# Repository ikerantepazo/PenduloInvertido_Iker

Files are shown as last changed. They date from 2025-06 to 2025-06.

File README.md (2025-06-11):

# PenduloInvertido_Iker
En este repositorio se encuentra tanto la práctica 4 cómo la práctica 6 de la asignatura de Teoría de Control

PRÁCTICA 4 - *PID en tiempo discreto*

Esta práctica tiene como objetivo implementar una biblioteca de controladores PID en tiempo discreto para ser utilizada en un microcontrolador ESP32, con aplicación directa en el control de un péndulo invertido. Esta biblioteca será utilizada en el desarrollo del proyecto de control descrito en el capítulo 6 del guión de prácticas.

Se desarrollarán tres variantes del controlador PID en tiempo discreto:

-PID : utiliza aproximaciones hacia atrás para las derivadas y sumas acumulativas para la integral.
-PID como filtro IIR: modelado mediante transformada Z, facilitando su implementación como filtro digital.
-PID filtro baja : se le pone un filtro al término derivativo para evitar que el ruido o los cambios bruscos del error afecten al control.

Cada implementación está basada en los pseudocódigos del guión.

Esta práctica está encapsulada en la carpeta libraries donde nos encontraremos :

I2Cdev/

Contiene archivos fuente y cabeceras que permiten la comunicación mediante el protocolo I2C. Es una biblioteca comúnmente usada para facilitar la lectura y escritura con sensores como el MPU6050

MPU6050/

Incluye las definiciones y funciones específicas para el sensor MPU6050, que proporciona mediciones de aceleración y giroscopio. Esta biblioteca se apoya en I2Cdev para obtener los datos del sensor y es esencial para calcular la posición y velocidad angular del péndulo.

PIDController/

Es la biblioteca desarrollada para está práctica para implementar los tres tipos de controladores PID discretos:

-PID directo
-PID como filtro IIR
-PID filtro pasa baja

Dentro de cada carpeta estarán los archivos .h y .cpp con la implementación de las clases PID

Se añadirá además una carpeta examples que contendrá tres ejemplos simples que muestran cómo usar cada una de las variantes del controlador PID implementadas.

CodigoCompletoPendulo.ino

Este es el sketch código principal de Arduino que integra las bibliotecas anteriores. Aquí se encuentra el código de control que:

-Lee el ángulo del péndulo usando el MPU6050
-Calcula la señal de control con el PID
-Aplica la corrección al actuador
-Permite probar y comparar las distintas variantes del controlador PID

PRÁCTICA 6 - **PENDULO INVERTIDO**

Iker Antepazo Cancelas 

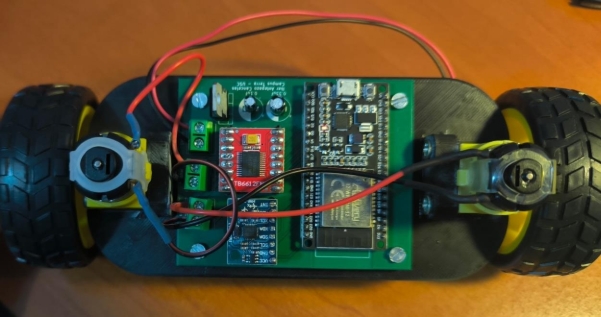
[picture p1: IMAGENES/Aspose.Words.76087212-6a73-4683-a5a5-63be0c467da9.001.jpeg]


**Introducción:**
**\
` `En este documento recogeremos el proceso llevado a cabo para la creación y construcción de un robot llamado “péndulo invertido”, cuya función será de tratar de mantenerse en posición vertical con una tolerancia de ±5◦. 

El sistema debe compensar los empujones externos y volver a la posición vertical y debe ser capaz de poder iniciar su funcionamiento desde cualquier posición. 

**Metodología seguida**

1. **Buscar proyectos similares:** Investigar si ya existe un proyecto de un robot similar que sea funcional y esté documentado. Tanto en respositorios de github como en mi caso en videos de la plataforma YouTube y en la página “grabcad”. 
1. **Investigación general:** Como no existe ningún proyecto bien hecho y bien documentado que esté completo, procedemos a investigar el modus operandi que trataremos de llevar a cabo el proyecto partiendo de las ideas que sacamos de los sitios web antes mencionados. 
3. **Fijación de objetivos:** Es importante la fijación de ciertas metas para saber qué hardware necesitamos. Tanto es así para nuestro chasis como para nuestra placa PCB. 
3. **Selección del Hardware:** Una vez que sabemos las metas que queremos lograr conseguir con nuestro robot, tenemos que buscar el hardware necesario que se adapte a la perfección con lo que necesitaremos. 
3. **Diseño de la PCB:** Deberemos crear desde 0 una placa PCB diseñada por KiCad que contenga los elementos que emplearemos para el robot y las pistas con los mismos elementos conectados entre sí a través de los pines. 
3. **Diseño del Chasis:** Deberemos resolver dos problemáticas: tener el peso compensado y tener el centro de gravedad bajo. 
3. **Prueba de componentes por separado:** Verificamos que todo funcione por separado para luego soldar todo en la placa. 
3. **Montaje:** Montamos todos los componentes en el chasis para poder probar el robot al completo. 
3. **Programación inicial:** Hacemos un primer código que solo mantenga el robot estático en un mismo lugar. 
3. **Ajuste del PID:** Ajustamos los valores del PID para que el robot se mantenga estático. 

**Objetivos**

**Estabilidad Perpendicular al Suelo:**  

Garantizar que el robot sea capaz de mantenerse estable en la posición perpendicular al suelo (vertical). ✔ 

**Compensación de Empujones:**  

Desarrollar la capacidad del robot para compensar empujones y así evitar las caídas. ✔ 

**Arranque desde Cualquier Posición:** Lograr que el robot pueda iniciar su funcionamiento desde cualquier posición inicial. ✔ 

**Reducción de Posibilidades de Volcar:** Minimizar las posibilidades de que el robot vuelque y se caiga y asegurar que el robot no pueda volver a una posición no deseada. ✔ 

**Investigación** 

En relación con la búsqueda de otros proyectos de este estilo, he detectado una problemática: hay varios proyectos hechos con el mismo principio, pero nadie ha creado una documentación completa y descriptiva del proyecto, esto conlleva a un mayor gasto y empleo de tiempo en la búsqueda de los elementos hardware que debemos comprar y buscar, al igual que para el desarrollo de la pcb empleada y del diseño del chasis. En parte tuve suerte ya que gracias a toda la información recopilada por las páginas web y gracias al trabajo del compañero Daniel Acevedo, que fue el primero en hacer este proyecto y gracias al cual he sacado adelante este robot. Aunque hay esta escasez de información, he podido rescatar algo de información examinando videos. De ellos, he determinado el hardware que se necesita y el tipo de control para manejar el movimiento (PID). 

**Hardware** 

Para la selección del hardware, se buscó que el robot se hiciera con elementos básicos y comunes para que sea un robot de bajo costo y no dependa de cierta solvencia para poder realizarse, ya que como no hay verdaderamente un informe completo y descriptivo de todos los pasos a seguir podría atascarse el proyecto y ser necesarias varias pruebas como fue mi caso. 

**ESP32:**  

Para el microcontrolador, he empleado una ESP32. En concreto, se ha utilizado una ESP32 que ronda los 11€ en Amazon. He consultado un par de páginas web para informarme al respecto de esta placa, y a continuación dejaré todo lo necesario a conocer sobre esta placa:[ ESP32 ](https://es.wikipedia.org/wiki/ESP32). 

Este elemento es el encargado de mediante una conexión con cable USB al ordenador en la aplicación de Arduino, recibir los programas empleados. 

**MPU-6050:**  

Este sensor tiene incorporado un acelerómetro y un giroscopio, los cuales vamos a usar para medir la orientación e inclinación del robot, que como hemos comentado al principio del documento buscamos que pueda mantener la verticalidad sin sobrepasar los 5 grados de inclinación angular. Las fórmulas e información necesaria que he necesitado para usar este sensor están en esta página web:[ MPU6050 ](https://invensense.tdk.com/wp-content/uploads/2015/02/MPU-6000-Datasheet1.pdf). 

En el caso de este componente tuve serios problemas para encontrarlo ya que lo compré tres veces, pero me daba errores al probarlo hasta que acabé encontrando el idóneo. 

**Condensadores:**  

Empleé dos condensadores, uno de 0.1 uF y otro de 0.22uF:[ 0,1uF ](https://www.microjpm.com/products/capacitor-electrolitico-0-1uf-50v/)[,0,22uF ](https://www.microjpm.com/products/capacitor-electrolitico-50v-0-22uf/)

**Bloques terminales:** 

En este aspecto emplee tres bloques terminales que fueron los encargados de conectarse con los motores y la batería. A continuación, dejaré un enlace para el acceso a sus características:[ Bloques terminales ](https://es.rs-online.com/web/b/wurth-elektronik/conectores/bloques-terminales/?displayMonolithBrandPage=true)

**TB6612FNG:**  

El driver que he elegido es una solución más moderna que el común puente H; su precio es de menos de 2€ y nos permite controlar 2 motores simultáneamente y de manera independiente. He seleccionado este componente al igual que los demás gracias a la documentación presentada por Daniel Acevedo. Al igual que con el anterior sensor, la página de la que extraje toda la información la dejo en el siguiente enlace:[ TB6612FNG ](https://cdn.sparkfun.com/assets/0/1/b/b/3/TB6612FNG.pdf)

**Batería:** En este aspecto he empleado un portapilas de 4 pilas AA conectadas a los bornes de la placa.[ Portapilas AA ](https://www.amazon.es/CABLEPELADO-Portapilas-Interruptor-Soporte-Bater%C3%ADa/dp/B0B8VN7ZGZ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)

**Motores y ruedas:**  

En este proyecto se han usado los comúnmente usados motores de DC con una reductora, la cual permite un fácil acople de una rueda que normalmente se vende con el propio motor.[ Motores y ruedas ](https://www.amazon.es/Gebildet-Motorreductor-Tracci%C3%B3n-Rob%C3%B3tico-Neum%C3%A1tico/dp/B08D39MFN1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) 

**Regulador de voltaje:** 

En este aspecto emplee un regulador de voltaje LM7805 que me servirá para 

controlar el flujo de voltaje en el circuito. Aquí dejaré una datasheet para  comprender su funcionamiento y características:[ Regulador de voltaje ](https://www.alldatasheet.com/view.jsp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)

**PCB** 

He diseñado una placa PCB capaz de emplear todos los elementos antes  

mencionados y que estén conectados entre sí de forma que nos funcione todo a   la perfección. En este aspecto debemos buscar la obtención de una placa que   no tenga mucho lío de pistas para ver la función de cada una de ellas a la   perfección, buscamos una claridad importante para en caso de alguna duda  presentada a la hora de la soldadura de los elementos con el estañador saber de   qué pin a qué otro pin va cada pista. 

Asímismo es de vital importancia el contar con una placa de pocas  

dismensiones para así facilitarnos el proceso de creación del chasis, porque no   queremos un robot muy grande, con lo cual esto será muy importante. 

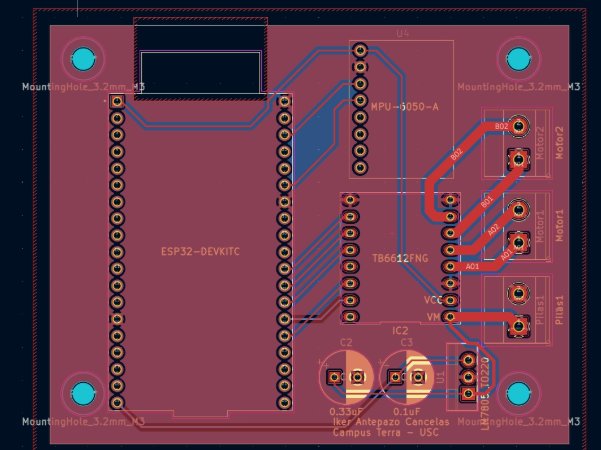
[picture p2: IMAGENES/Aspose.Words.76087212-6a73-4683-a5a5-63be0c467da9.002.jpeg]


**Chasis**

He diseñado 2 tipos de chasis para el robot el primero fue para tantear más o menos, y con el segundo, gracias a los consejos de Daniel he logrado hacer funcionar el robot ya que cumple correctamente con los requisitos del centro del centro de gravedad que estaba muy centrado y a una altura baja, lo que proporcionaba una gran estabilidad.  

Lo importante a tener en cuenta para el desarrollo del chasis son los siguientes dos requisitos: 

**Centro de gravedad:** Es determinante que el centro de gravedad del robot sea el más bajo posible. Si el peso está muy elevado respecto al suelo, se hará prácticamente imposible que el robot sea capaz de mantenerse derecho. 

**Peso centrado:** Al igual que el centro de gravedad bajo, es decisivo que el peso del robot esté centrado en el eje de las ruedas, lo que hará que, combinado con el apartado anterior, el robot debería mantenerse en la posición que queremos sin necesidad de que el robot esté encendido. Cuanto más estable sea el robot gracias al diseño del chasis, más sencillo nos será ajustar el PID hasta lograr que el robot funcione correctamente. Ahora voy a explicar los problemas de mis distintos chasis hasta el momento en que fui capaz de hacer que el robot funcionara. 

***Primer chasis:*** 

Después de corregir los errores de los dos chasis mencionados por Daniel Acevedo en su documentación, logré hacer un chasis con el que robot funcionara. En este caso, el centro de gravedad estaba muy centrado y a una altura baja, lo que proporcionaba una gran estabilidad incluso cuando el robot estaba apagado. Pero no se adaptaba completamente con mis necesidades debido al uso de los motores antes mencionados. 

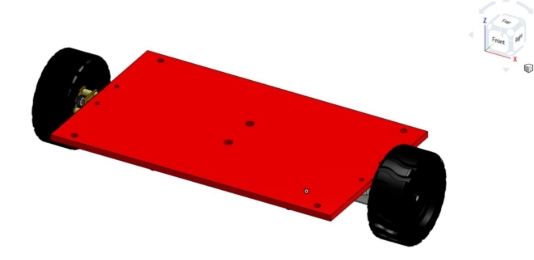
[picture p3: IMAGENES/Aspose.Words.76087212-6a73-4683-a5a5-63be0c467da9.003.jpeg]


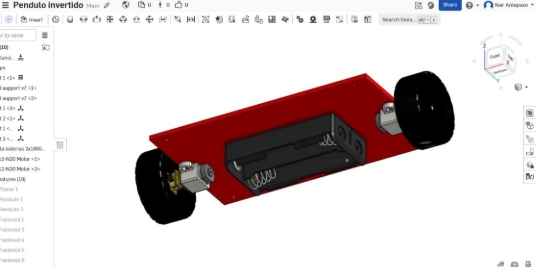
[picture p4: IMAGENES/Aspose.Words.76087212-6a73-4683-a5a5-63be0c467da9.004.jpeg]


Este primer chasis lo he desarrollado a través de la página web de ”onshape” lo que me permitió diseñar incluso el portapilas pero se me hizo muy duro y difícil terminar con este proceso con lo cual para el segundo chasis me pasé a FreeCad. 

***Segundo chasis:*** 

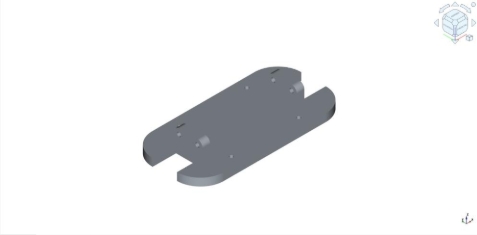
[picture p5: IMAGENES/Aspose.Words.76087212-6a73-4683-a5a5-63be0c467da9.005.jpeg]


Este segundo chasis lo he diseñado con la ayuda de FreeCad, le he agregado   calculando las dimensiones de la placa PCB unos agujeros para permitirnos   atornillar la placa al chasis con tuercas y tornillos asegurándonos así la fijación   de esta. Al igual que esta novedad también le he agregado unas elevaciones en   los laterales de la placa para poder atornillar nuestros motores en posición    vertical permitiéndonos de este modo emplear los motores tradicionales antes  mencionados. 

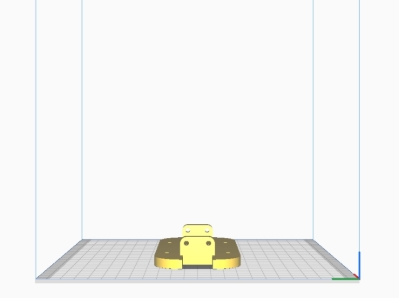
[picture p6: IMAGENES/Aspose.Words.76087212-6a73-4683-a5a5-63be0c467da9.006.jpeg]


Este fue el diseño final del chasis ya que se adaptaba a la perfección con lo  

deseado, con lo cual generamos el archivo .gcode para enviar a la impresora 3d.   Esto se hizo gracias a la aplicación Ultimaker Cura. 

A partir de aquí la impresión duró 4 horas aproximadamente, pero tuve  bastantes problemas con las impresoras del centro debido a que se quedaba atascado el material y había ciertos errores de calibración en la impresora 

empleada. 

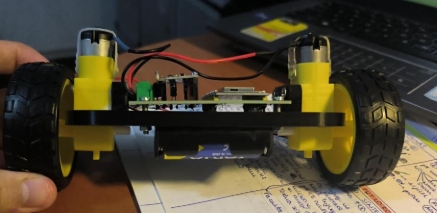
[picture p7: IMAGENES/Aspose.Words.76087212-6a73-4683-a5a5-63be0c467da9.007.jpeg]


**Prueba de componentes por separado** 

**MPU-6050:** 

Realizamos una primera prueba para verificar que el sensor funcione 

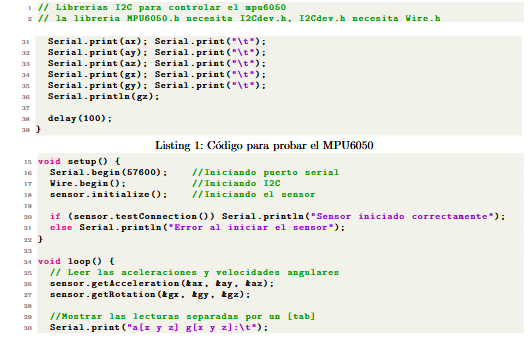
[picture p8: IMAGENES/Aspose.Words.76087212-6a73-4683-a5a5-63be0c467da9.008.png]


Como vemos que el sensor nos proporciona medidas coherentes, procedemos  a calibrar el sensor en la posición en la que estará midiendo. 

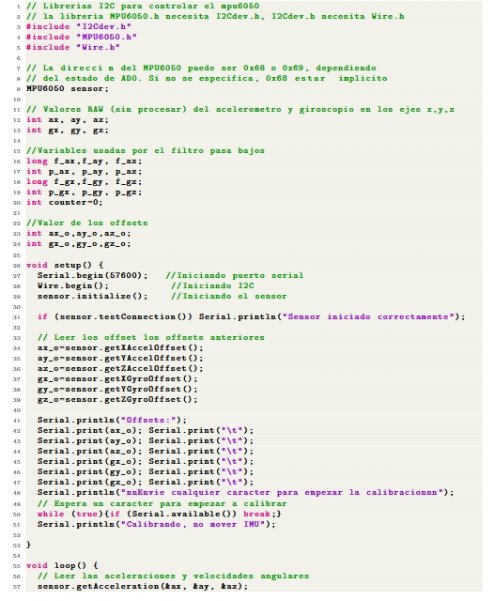
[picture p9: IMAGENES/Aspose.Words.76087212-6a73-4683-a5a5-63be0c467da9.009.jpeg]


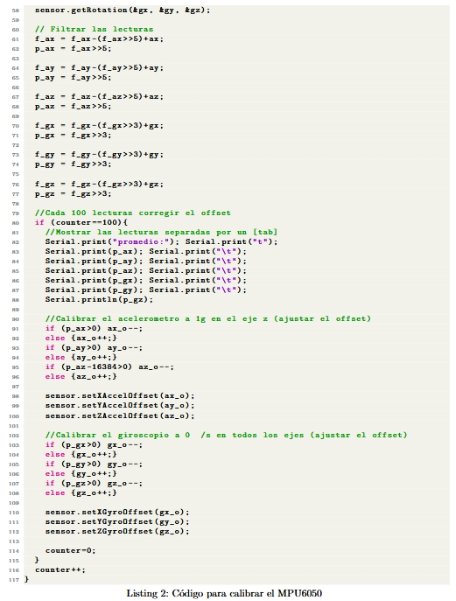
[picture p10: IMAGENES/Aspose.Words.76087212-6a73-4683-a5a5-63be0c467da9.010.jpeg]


Finalmente, probamos el código que utilizaremos para medir el ángulo de 

inclinación del robot. 



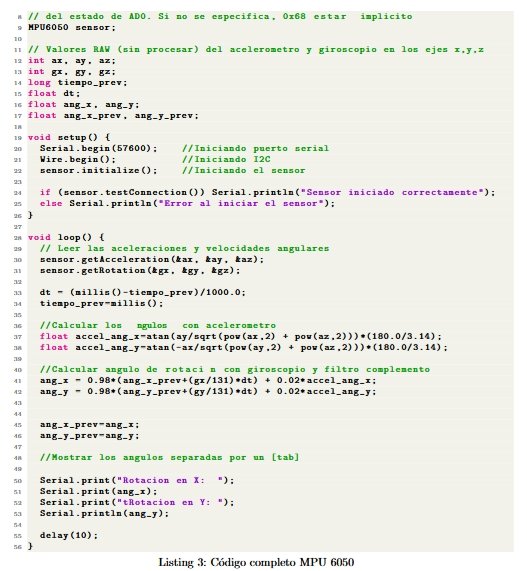
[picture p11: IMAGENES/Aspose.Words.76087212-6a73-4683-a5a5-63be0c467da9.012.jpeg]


TB6612FNG: 

Al igual que los códigos del sensor anterior, los he modificado antes de subirlos   a la ESP32, ajustando los pines para que sean compatibles con la ESP32: 

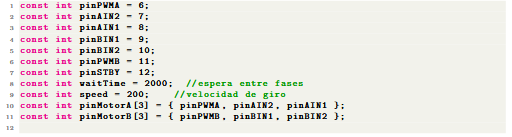
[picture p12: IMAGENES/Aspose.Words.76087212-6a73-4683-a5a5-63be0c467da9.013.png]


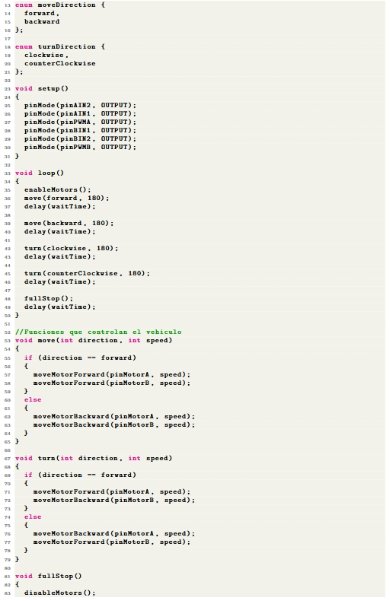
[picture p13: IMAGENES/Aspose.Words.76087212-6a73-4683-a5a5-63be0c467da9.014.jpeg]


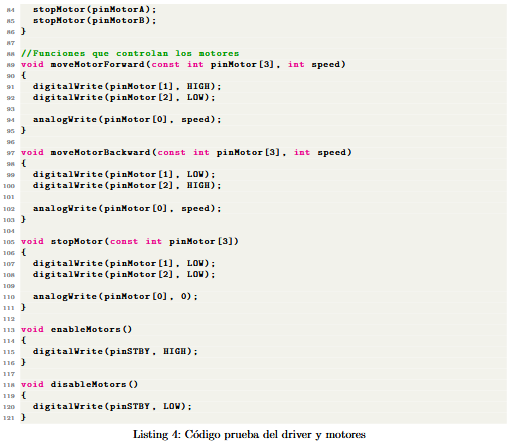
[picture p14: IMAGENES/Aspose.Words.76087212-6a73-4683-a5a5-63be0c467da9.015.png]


**Montaje** 

El montaje es muy simple, debemos conectar todo de la manera en la que hemos diseñado la PCB. Además de las conexiones de los sensores, 

necesitamos alimentar los motores y la ESP32.  Ambos trabajan a voltajes   distintos, por lo que requerimos un regulador de voltaje. Los motores los he   alimentado a 9V, y la ESP32 se alimenta a 5V en el pin 5V.  

**Ajuste del PID** 

Para poder ajustar el PID, es necesario comprender la función de cada una de   las tres componentes de este sistema de control. 

**Empezar desde 0:** 

Es crucial comenzar con todos los valores desde 0 y ajustar los valores de 

manera ordenada e independiente. 

**Orden de calibración:** 

Se recomienda iniciar ajustando los valores de Kp hasta lograr que el robot sea   capaz de levantarse desde el suelo. Una vez logrado esto, se anota el valor optimo y se establece la variable a 0. 

Luego, se ajusta Kd, buscando un valor en el cual el robot no oscile  exageradamente y casi se mantenga en la posición deseada. 

En el tercer paso, se restablece Kp al valor anotado anteriormente y se deja Kd   en el valor optimo encontrado. En este punto, Ki aun se mantiene en 0, pero primero se verifica que el robot casi se mantenga en la posición 

deseada. 

Finalmente, se ajusta Ki. Esta componente solo ayuda al robot a alcanzar la posición precisa, si las otras dos componentes no se han ajustado 

correctamente, Ki no cambiara radicalmente el comportamiento del robot. En   resumen, Kp y Ki son las más importantes. 

**Valores pequeños:** 

Los valores del PID dependen en gran medida de la construcción del robot. Es   importante tener en cuenta que cuanto mayores sean los valores, más agresivo   será el movimiento del robot. Se 

recomienda comenzar con valores menores a 1 y realizar incrementos pequeños   para evitar que 

el robot se mueva bruscamente. 

**Programación inicial** 

Al combinar los códigos previamente agregados a esta documentación con un   control PID, podemos lograr que el robot funcione. Sin embargo, es necesario 

ajustar los valores del PID para que se adapten a nuestro caso específico. 

En este punto fue donde en mi caso el robot dejó de funcionar, esto debido a que   debe haber alguna conexión en la placa que hace que la ESP32 se quede 

congelada y no acabe de enviar el programa el componente pertinente. Trataré   de solucionar este problema más adelante por mi cuenta, pero debido al cierre   de actas cercano aquí es dónde me he quedado. 

El código que deberíamos emplear sería: 

--------------------> (Está completo y descriptivo en el pdf)

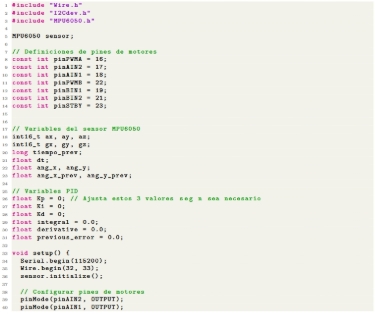
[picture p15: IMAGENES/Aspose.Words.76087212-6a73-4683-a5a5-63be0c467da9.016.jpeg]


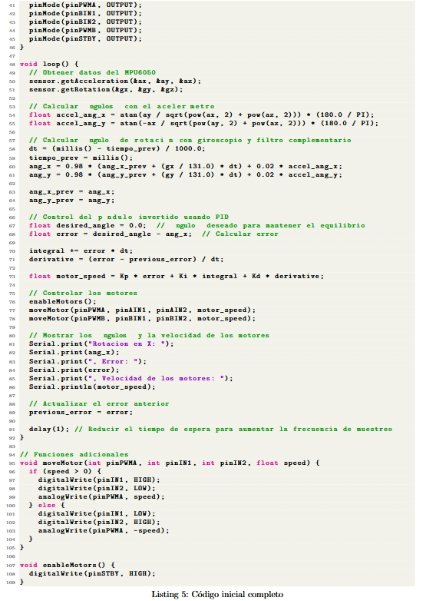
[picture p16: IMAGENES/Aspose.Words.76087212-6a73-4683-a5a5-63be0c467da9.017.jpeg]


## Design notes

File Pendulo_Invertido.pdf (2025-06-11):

## PENDULO INVERTIDO

Iker Antepazo Cancelas

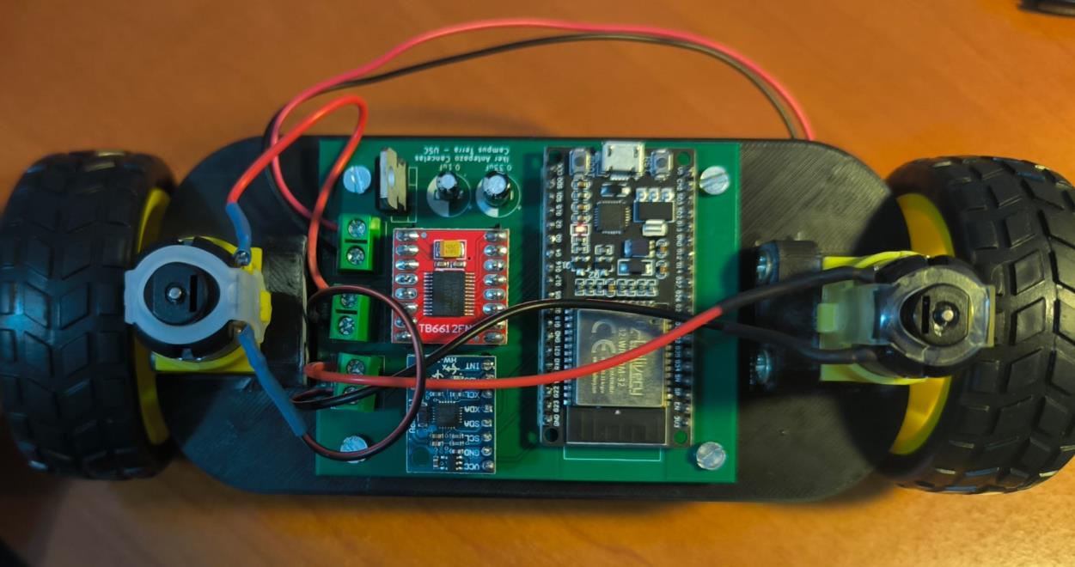
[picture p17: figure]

# Introducción:

En este documento recogeremos el proceso llevado a cabo para la creación y construcción de un robot llamado “péndulo invertido”, cuya función será de tratar de mantenerse en posición vertical con una tolerancia de ±5◦.
El sistema debe compensar los empujones externos y volver a la posición vertical y debe ser capaz de poder iniciar su funcionamiento desde cualquier posición.

# Metodología seguida

1. Buscar proyectos similares: Investigar si ya existe un proyecto de un robot similar que sea funcional y esté documentado. Tanto en respositorios de github como en mi caso en videos de la plataforma YouTube y en la página “grabcad”.
2. Investigación general: Como no existe ningún proyecto bien hecho y bien documentado que esté completo, procedemos a investigar el modus operandi que trataremos de llevar a cabo el proyecto partiendo de las ideas que sacamos de los sitios web antes mencionados.

3. Fijación de objetivos: Es importante la fijación de ciertas metas para saber qué hardware necesitamos. Tanto es así para nuestro chasis como para nuestra placa PCB.
4. Selección del Hardware: Una vez que sabemos las metas que queremos lograr conseguir con nuestro robot, tenemos que buscar el hardware necesario que se adapte a la perfección con lo que necesitaremos.
5. Diseño de la PCB: Deberemos crear desde 0 una placa PCB diseñada por KiCad que contenga los elementos que emplearemos para el robot y las pistas con los mismos elementos conectados entre sí a través de los pines.
6. Diseño del Chasis: Deberemos resolver dos problemáticas: tener el peso compensado y tener el centro de gravedad bajo.
7. Prueba de componentes por separado: Verificamos que todo funcione por separado para luego soldar todo en la placa.
8. Montaje: Montamos todos los componentes en el chasis para poder probar el robot al completo.
9. Programación inicial: Hacemos un primer código que solo mantenga el robot estático en un mismo lugar.

10.Ajuste del PID: Ajustamos los valores del PID para que el robot se mantenga estático.

# Objetivos

Estabilidad Perpendicular al Suelo:
Garantizar que el robot sea capaz de mantenerse estable en la posición perpendicular al suelo (vertical). ✔

Compensación de Empujones:
Desarrollar la capacidad del robot para compensar empujones y así evitar las caídas. ✔

Arranque desde Cualquier Posición: Lograr que el robot pueda iniciar su funcionamiento desde cualquier posición inicial. ✔

Reducción de Posibilidades de Volcar: Minimizar las posibilidades de que el robot vuelque y se caiga y asegurar que el robot no pueda volver a una posición no deseada. ✔

# Investigación

En relación con la búsqueda de otros proyectos de este estilo, he detectado una problemática: hay varios proyectos hechos con el mismo principio, pero nadie ha creado una documentación completa y descriptiva del proyecto, esto conlleva a un mayor gasto y empleo de tiempo en la búsqueda de los elementos hardware que debemos comprar y buscar, al igual que para el desarrollo de la pcb empleada y del diseño del chasis. En parte tuve suerte ya que gracias a toda la información recopilada por las páginas web y gracias al trabajo del compañero Daniel Acevedo, que fue el primero en hacer este proyecto y gracias al cual he sacado adelante este robot. Aunque hay esta escasez de información, he podido rescatar algo de información examinando videos. De ellos, he determinado el hardware que se necesita y el tipo de control para manejar el movimiento (PID).

# Hardware

Para la selección del hardware, se buscó que el robot se hiciera con elementos básicos y comunes para que sea un robot de bajo costo y no dependa de cierta solvencia para poder realizarse, ya que como no hay verdaderamente un informe completo y descriptivo de todos los pasos a seguir podría atascarse el proyecto y ser necesarias varias pruebas como fue mi caso.

ESP32:
Para el microcontrolador, he empleado una ESP32. En concreto, se ha utilizado una ESP32 que ronda los 11€ en Amazon. He consultado un par de páginas web para informarme al respecto de esta placa, y a continuación dejaré todo lo necesario a conocer sobre esta placa: ESP32 (https://es.wikipedia.org/wiki/ESP32) .
Este elemento es el encargado de mediante una conexión con cable USB al ordenador en la aplicación de Arduino, recibir los programas empleados.

MPU-6050:
Este sensor tiene incorporado un acelerómetro y un giroscopio, los cuales vamos a usar para medir la orientación e inclinación del robot, que como hemos comentado al principio del documento buscamos que pueda mantener la verticalidad sin sobrepasar los 5 grados de inclinación angular. Las fórmulas e información necesaria que he necesitado para usar este sensor están en esta página web: MPU6050 (https://invensense.tdk.com/wp-content/uploads/2015/02/MPU-6000-Datasheet1.pdf) .

En el caso de este componente tuve serios problemas para encontrarlo ya que lo compré tres veces, pero me daba errores al probarlo hasta que acabé encontrando el idóneo.

Condensadores:
Empleé dos condensadores, uno de 0.1 uF y otro de 0.22uF: 0,1uF (https://www.microjpm.com/products/capacitor-electrolitico-0-1uf-50v/) ,0,22uF (https://www.microjpm.com/products/capacitor-electrolitico-50v-0-22uf/)

Bloques terminales:
En este aspecto emplee tres bloques terminales que fueron los encargados de conectarse con los motores y la batería. A continuación, dejaré un enlace para el acceso a sus características: Bloques terminales (https://es.rs-online.com/web/b/wurth-elektronik/conectores/bloques-terminales/?displayMonolithBrandPage=true)

TB6612FNG:
El driver que he elegido es una solución más moderna que el común puente H; su precio es de menos de 2€ y nos permite controlar 2 motores simultáneamente y de manera independiente. He seleccionado este componente al igual que los demás gracias a la documentación presentada por Daniel Acevedo. Al igual que con el anterior sensor, la página de la que extraje toda la información la dejo en el siguiente enlace: TB6612FNG (https://cdn.sparkfun.com/assets/0/1/b/b/3/TB6612FNG.pdf)

Batería: En este aspecto he empleado un portapilas de 4 pilas AA conectadas a los bornes de la placa. Portapilas AA (https://www.amazon.es/CABLEPELADO-Portapilas-Interruptor-Soporte-Bater%C3%ADa/dp/B0B8VN7ZGZ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)

Motores y ruedas:
En este proyecto se han usado los comúnmente usados motores de DC con una reductora, la cual permite un fácil acople de una rueda que normalmente se vende con el propio motor. Motores y ruedas (https://www.amazon.es/Gebildet-Motorreductor-Tracci%C3%B3n-Rob%C3%B3tico-Neum%C3%A1tico/dp/B08D39MFN1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)

Regulador de voltaje:
En este aspecto emplee un regulador de voltaje LM7805 que me servirá para controlar el flujo de voltaje en el circuito. Aquí dejaré una datasheet para comprender su funcionamiento y características: Regulador de voltaje (https://www.alldatasheet.com/view.jsp?Searchword=Lm7805%20datasheet&gad_source=1&gad_campaignid=1421144141)

# PCB

He diseñado una placa PCB capaz de emplear todos los elementos antes mencionados y que estén conectados entre sí de forma que nos funcione
todo a | la perfección. En este aspecto debemos buscar la obtención de una
placa que | no tenga mucho lío de pistas para ver la función de cada una de ellas a
la | perfección, buscamos una claridad importante para en caso de alguna
duda presentada a la hora de la soldadura de los elementos con el estañador saber de qué pin a qué otro pin va cada pista.

Asímismo es de vital importancia el contar con una placa de pocas
dismensiones para así facilitarnos el proceso de creación del chasis, porque no queremos un robot muy grande, con lo cual esto será muy importante.

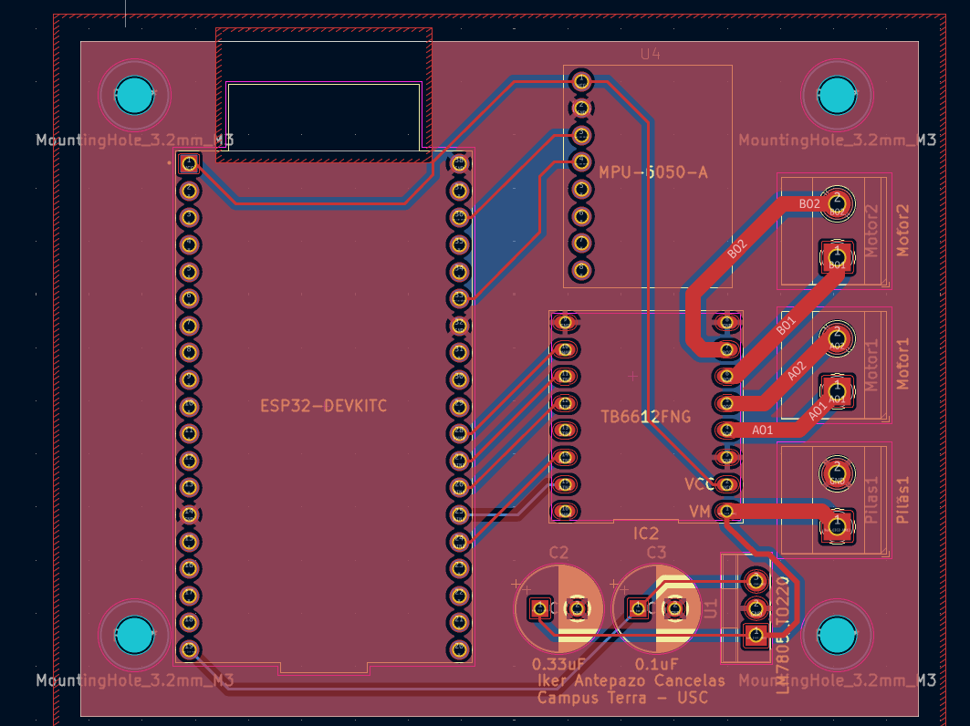
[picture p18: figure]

# Chasis

He diseñado 2 tipos de chasis para el robot el primero fue para tantear más o menos, y con el segundo, gracias a los consejos de Daniel he logrado hacer funcionar el robot ya que cumple correctamente con los requisitos del centro del centro de gravedad que estaba muy centrado y a una altura baja, lo que proporcionaba una gran estabilidad.

Lo importante a tener en cuenta para el desarrollo del chasis son los siguientes dos requisitos:

Centro de gravedad: Es determinante que el centro de gravedad del robot sea el más bajo posible. Si el peso está muy elevado respecto al suelo, se hará prácticamente imposible que el robot sea capaz de mantenerse derecho.

Peso centrado: Al igual que el centro de gravedad bajo, es decisivo que el peso del robot esté centrado en el eje de las ruedas, lo que hará que, combinado con el apartado anterior, el robot debería mantenerse en la posición que queremos sin necesidad de que el robot esté encendido. Cuanto más estable sea el robot gracias al diseño del chasis, más sencillo nos será ajustar el PID hasta lograr que el robot funcione correctamente. Ahora voy a explicar los problemas de mis distintos chasis hasta el momento en que fui capaz de hacer que el robot funcionara.

Primer chasis:
Después de corregir los errores de los dos chasis mencionados por Daniel Acevedo en su documentación, logré hacer un chasis con el que robot funcionara. En este caso, el centro de gravedad estaba muy centrado y a una altura baja, lo que proporcionaba una gran estabilidad incluso cuando el robot estaba apagado. Pero no se adaptaba completamente con mis necesidades debido al uso de los motores antes mencionados.

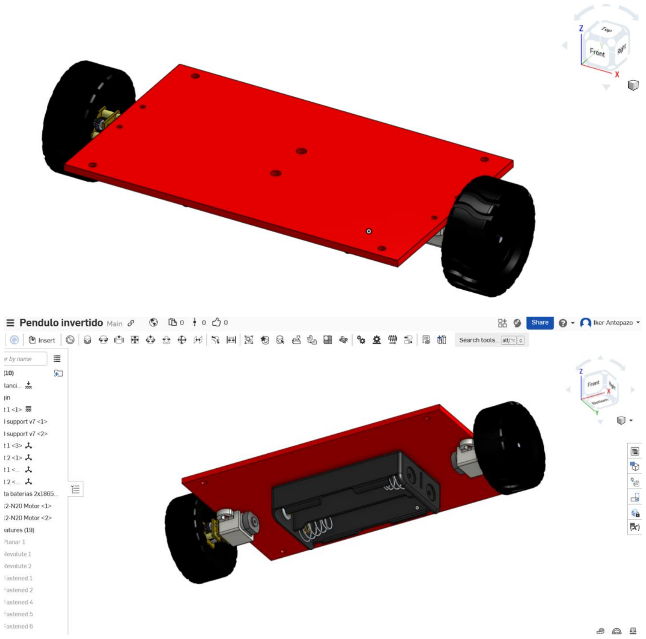
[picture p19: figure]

Este primer chasis lo he desarrollado a través de la página web de ”onshape” lo que me permitió diseñar incluso el portapilas pero se me hizo muy duro y difícil terminar con este proceso con lo cual para el segundo chasis me pasé a FreeCad.

Segundo chasis:

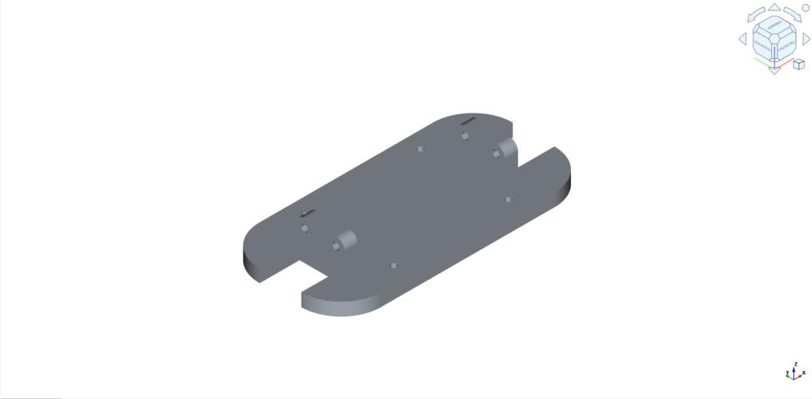
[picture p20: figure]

Este segundo chasis lo he diseñado con la ayuda de FreeCad, le he agregado calculando las dimensiones de la placa PCB unos agujeros para permitirnos atornillar la placa al chasis con tuercas y tornillos asegurándonos así la
fijación | de esta. Al igual que esta novedad también le he agregado unas
elevaciones en | los laterales de la placa para poder atornillar nuestros motores
en posición | vertical permitiéndonos de este modo emplear los motores
tradicionales antes mencionados.

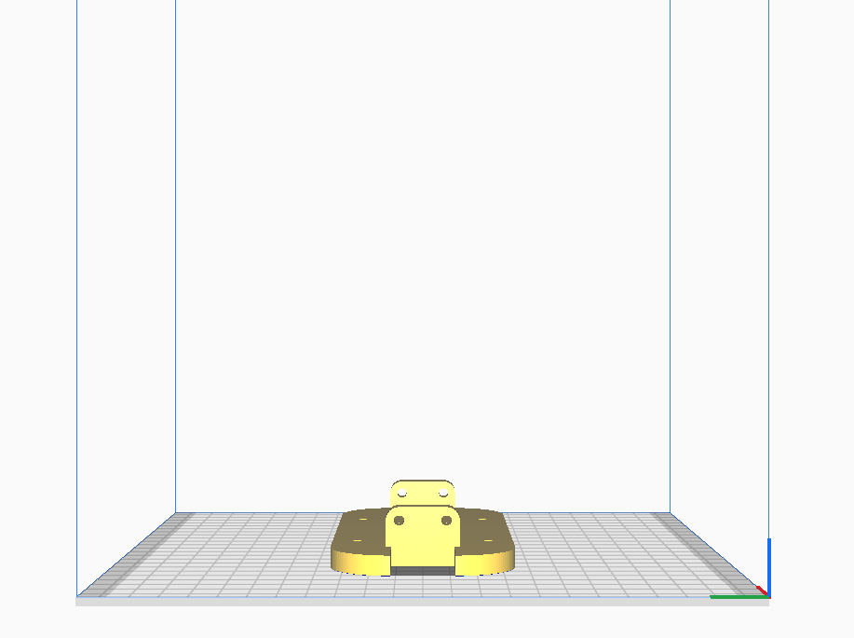
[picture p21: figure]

Este fue el diseño final del chasis ya que se adaptaba a la perfección con lo deseado, con lo cual generamos el archivo .gcode para enviar a la impresora
3d. | Esto se hizo gracias a la aplicación Ultimaker Cura.
| A partir de aquí la impresión duró 4 horas aproximadamente, pero tuve
| bastantes problemas con las impresoras del centro debido a que se quedaba
| atascado el material y había ciertos errores de calibración en la impresora
| empleada.

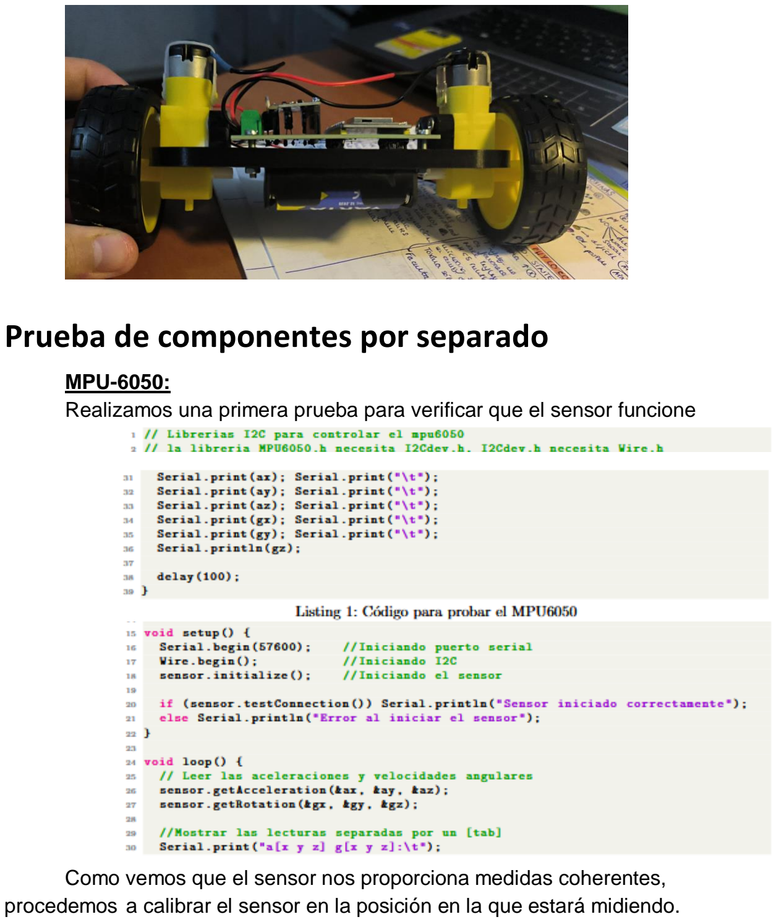
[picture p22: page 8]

# Prueba de componentes por separado

MPU-6050:
Realizamos una primera prueba para verificar que el sensor funcione

Como vemos que el sensor nos proporciona medidas coherentes, procedemos a calibrar el sensor en la posición en la que estará midiendo.

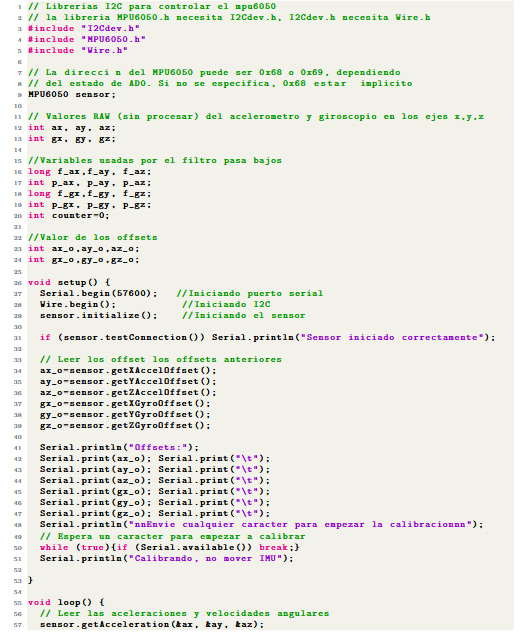
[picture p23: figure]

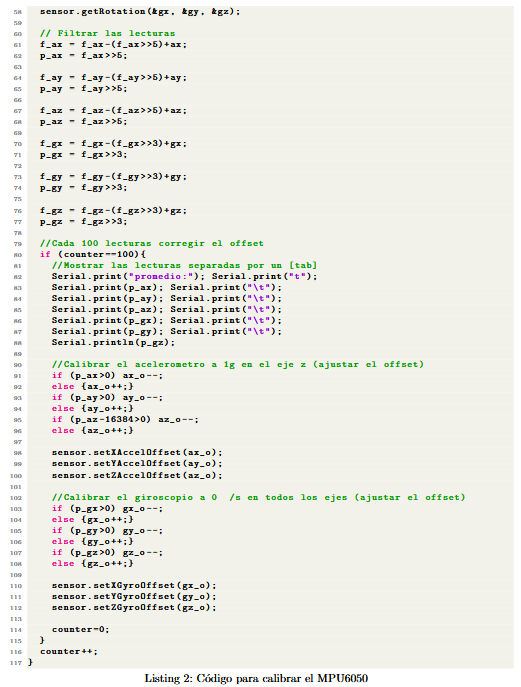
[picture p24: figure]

Finalmente, probamos el código que utilizaremos para medir el ángulo de inclinación del robot.

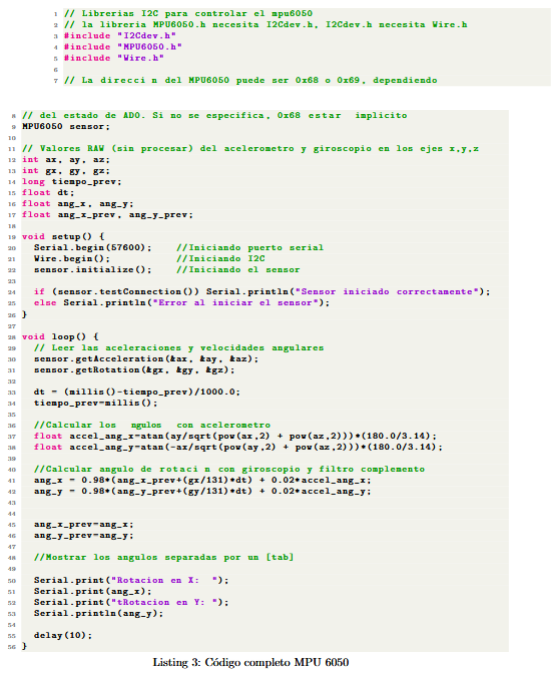
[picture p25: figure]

TB6612FNG:
Al igual que los códigos del sensor anterior, los he modificado antes de subirlos a la ESP32, ajustando los pines para que sean compatibles con la ESP32:

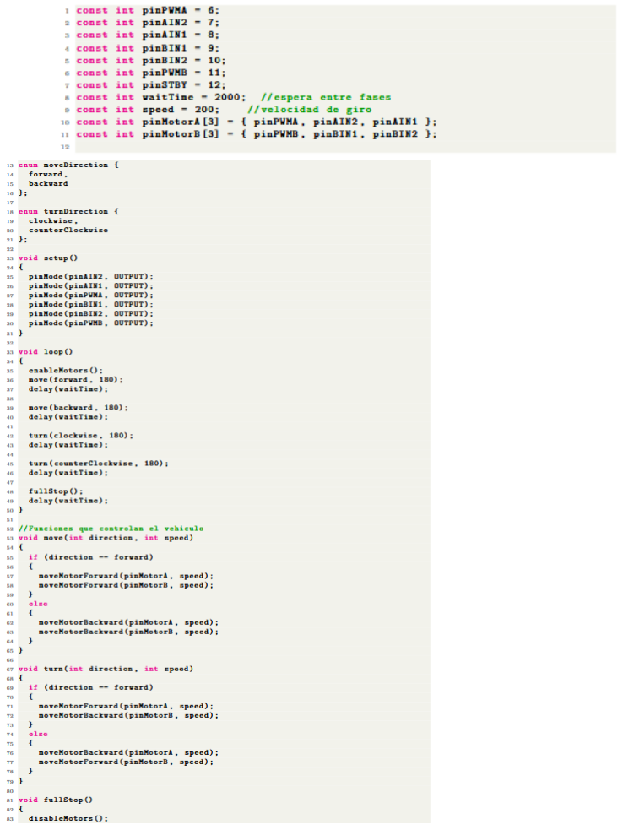
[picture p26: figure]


# Montaje

El montaje es muy simple, debemos conectar todo de la manera en la que hemos diseñado la PCB. Además de las conexiones de los sensores, necesitamos alimentar los motores y la ESP32. Ambos trabajan
a voltajes | distintos, por lo que requerimos un regulador de voltaje. Los
motores los he | alimentado a 9V, y la ESP32 se alimenta a 5V en el pin
5V.

# Ajuste del PID

Para poder ajustar el PID, es necesario comprender la función de cada una de las tres componentes de este sistema de control.
Empezar desde 0:
Es crucial comenzar con todos los valores desde 0 y ajustar los valores de manera ordenada e independiente.
Orden de calibración:
Se recomienda iniciar ajustando los valores de Kp hasta lograr que el robot sea capaz de levantarse desde el suelo. Una vez logrado esto, se anota el valor optimo y se establece la variable a 0.

Luego, se ajusta Kd, buscando un valor en el cual el robot no oscile exageradamente y casi se mantenga en la posición deseada.
En el tercer paso, se restablece Kp al valor anotado anteriormente y se deja Kd en el valor optimo encontrado. En este punto, Ki aun se mantiene en 0, pero primero se verifica que el robot casi se mantenga en la posición deseada.
Finalmente, se ajusta Ki. Esta componente solo ayuda al robot a alcanzar la posición precisa, si las otras dos componentes no se han ajustado correctamente, Ki no cambiara radicalmente el comportamiento
del robot. En | resumen, Kp y Ki son las más importantes.
Valores pequeños:
Los valores del PID dependen en gran medida de la construcción del robot.
Es | importante tener en cuenta que cuanto mayores sean los valores, más
agresivo | será el movimiento del robot. Se
recomienda comenzar con valores menores a 1 y realizar incrementos pequeños para evitar que
el robot se mueva bruscamente.

# Programación inicial

Al combinar los códigos previamente agregados a esta documentación con un control PID, podemos lograr que el robot funcione. Sin embargo, es necesario ajustar los valores del PID para que se adapten a nuestro caso específico.

En este punto fue donde en mi caso el robot dejó de funcionar, esto debido a que debe haber alguna conexión en la placa que hace que la ESP32 se quede congelada y no acabe de enviar el programa el componente pertinente.
Trataré | de solucionar este problema más adelante por mi cuenta, pero debido
al cierre | de actas cercano aquí es dónde me he quedado.

El código que deberíamos emplear sería:

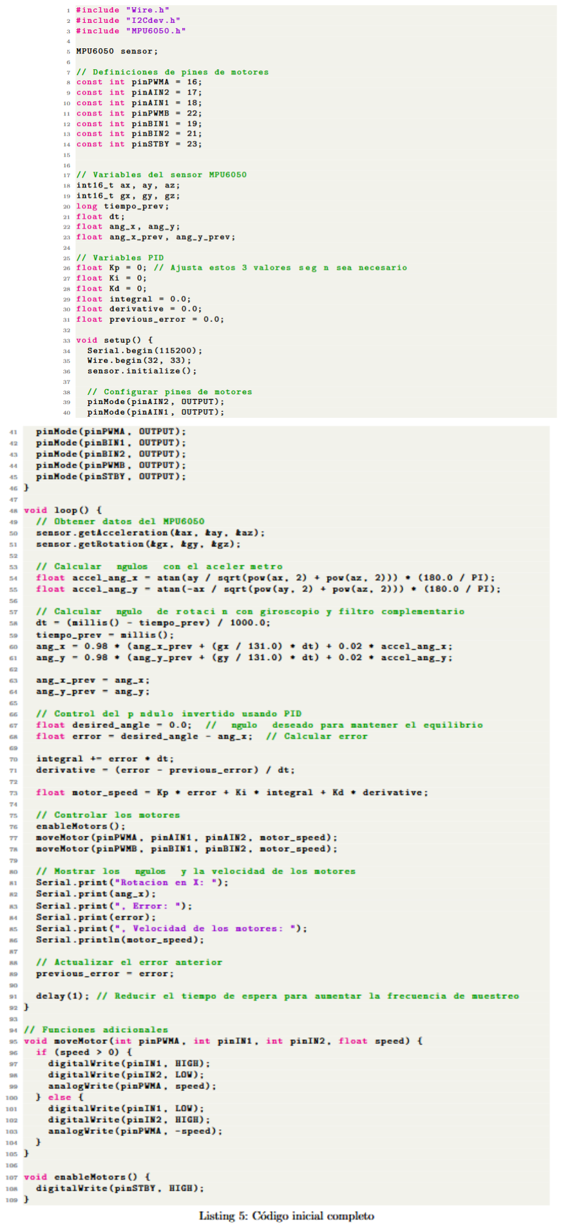
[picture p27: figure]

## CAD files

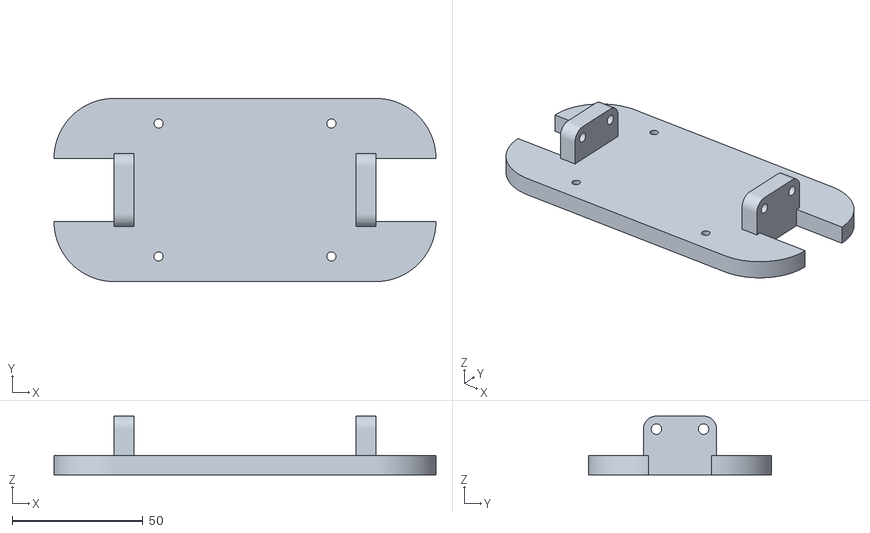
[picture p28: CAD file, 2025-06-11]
Pendulo_Inverso-Cuerpo.stl
146.0 x 70.0 x 22.5

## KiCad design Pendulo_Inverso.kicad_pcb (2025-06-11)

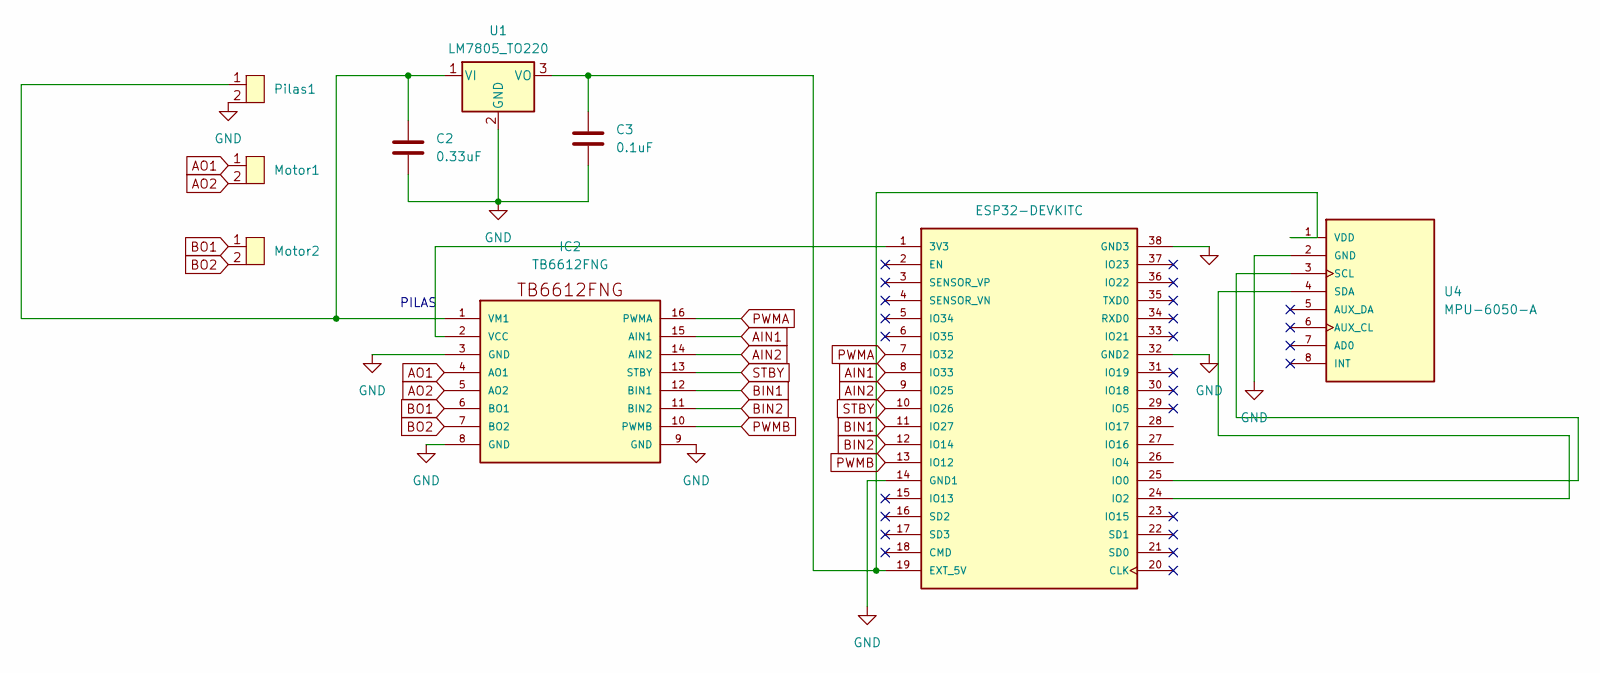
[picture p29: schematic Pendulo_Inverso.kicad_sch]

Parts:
C2: 0.33uF; CP_Radial_D8.0mm_P3.50mm
C3: 0.1uF; CP_Radial_D8.0mm_P3.50mm
IC2: TB6612FNG; TB6612FngSparkfun
Motor1, Motor2: TerminalBlock_Phoenix_MKDS-1,5-2_1x02_P5.00mm_Horizontal
Pilas1: TerminalBlock_Phoenix_MKDS-1,5-2_1x02_P5.00mm_Horizontal
U1: LM7805_TO220; TO-220-3_Vertical
U2: ESP32-DEVKITC; MODULE_ESP32-DEVKITC; PARTREV N/A
U4: MPU-6050-A; MPU6050; PARTREV 3.4

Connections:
AIN1: IC2.15 (AIN1), U2.8 (IO33)
AIN2: IC2.14 (AIN2), U2.9 (IO25)
AO1: IC2.4 (AO1), Motor1.1
AO2: IC2.5 (AO2), Motor1.2
BIN1: IC2.12 (BIN1), U2.11 (IO27)
BIN2: IC2.11 (BIN2), U2.12 (IO14)
BO1: IC2.6 (BO1), Motor2.1
BO2: IC2.7 (BO2), Motor2.2
GND: C2.2, C3.2, IC2.3 (GND), IC2.8 (GND), IC2.9 (GND), Pilas1.2, U1.2 (GND), U2.14 (GND1), U2.32 (GND2), U2.38 (GND3), U4.2 (GND)
unnamed: IC2.2 (VCC), U2.1 (3V3)
unnamed: C2.1, IC2.1 (VM1), Pilas1.1, U1.1 (VI)
unnamed: C3.1, U1.3 (VO), U2.19 (EXT_5V), U4.1 (VDD)
unnamed: U2.25 (IO0), U4.3 (SCL)
unnamed: U2.24 (IO2), U4.4 (SDA)
PWMA: IC2.16 (PWMA), U2.7 (IO32)
PWMB: IC2.10 (PWMB), U2.13 (IO12)
STBY: IC2.13 (STBY), U2.10 (IO26)

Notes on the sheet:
PILAS

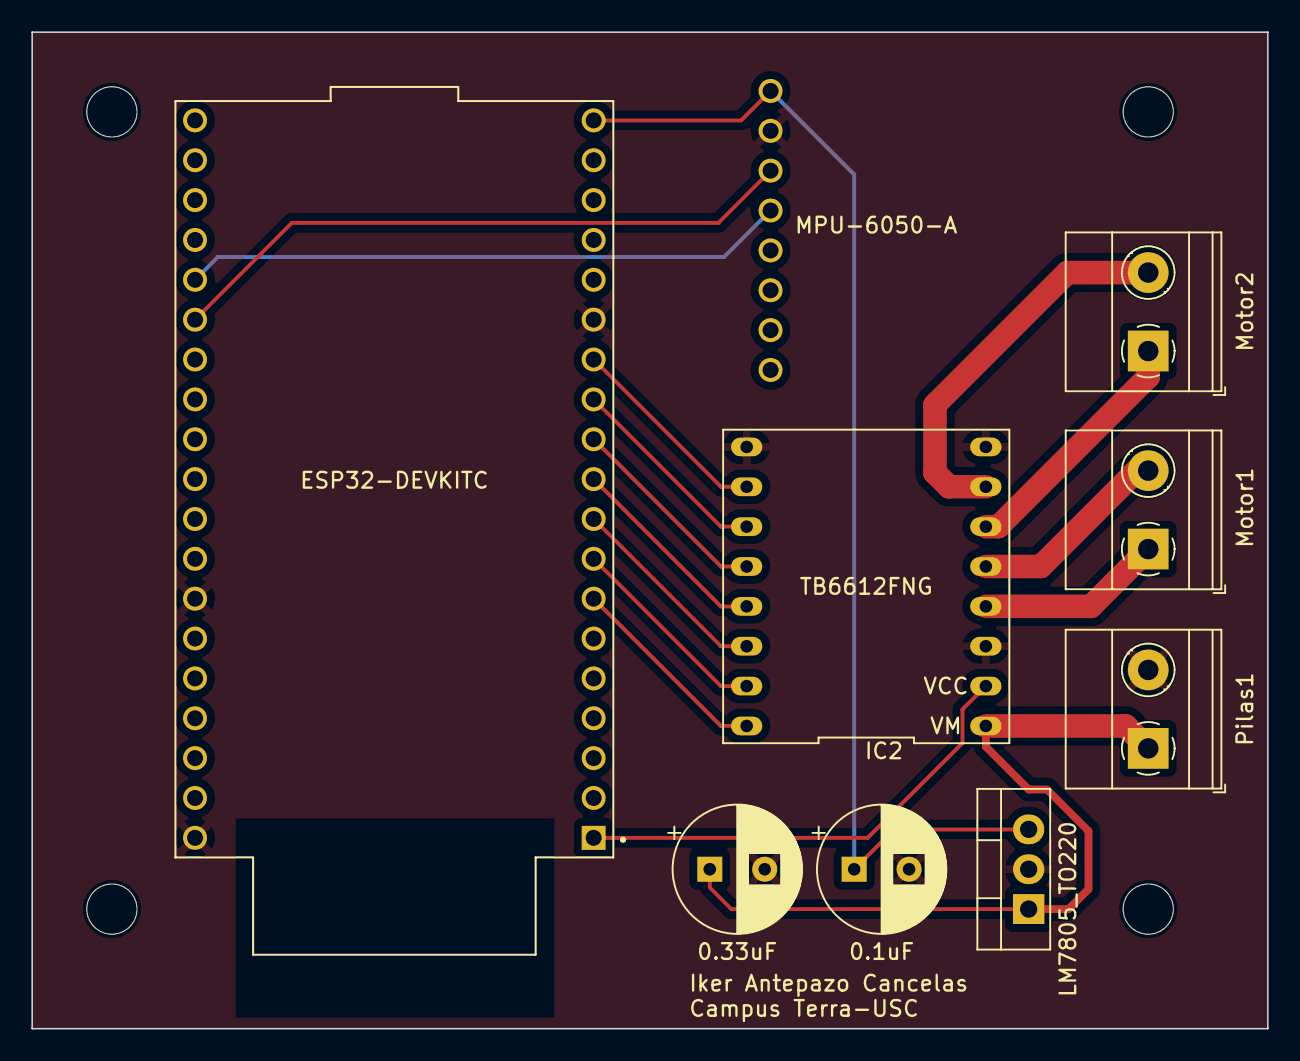
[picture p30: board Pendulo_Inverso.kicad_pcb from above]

Board: 2 copper layers, 78.7 x 63.5 mm, 9 parts (0 on the bottom side), 17 nets.
